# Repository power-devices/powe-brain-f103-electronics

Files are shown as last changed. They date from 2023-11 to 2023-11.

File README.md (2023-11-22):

# Welcome to the Power BrainF103 electronics repository

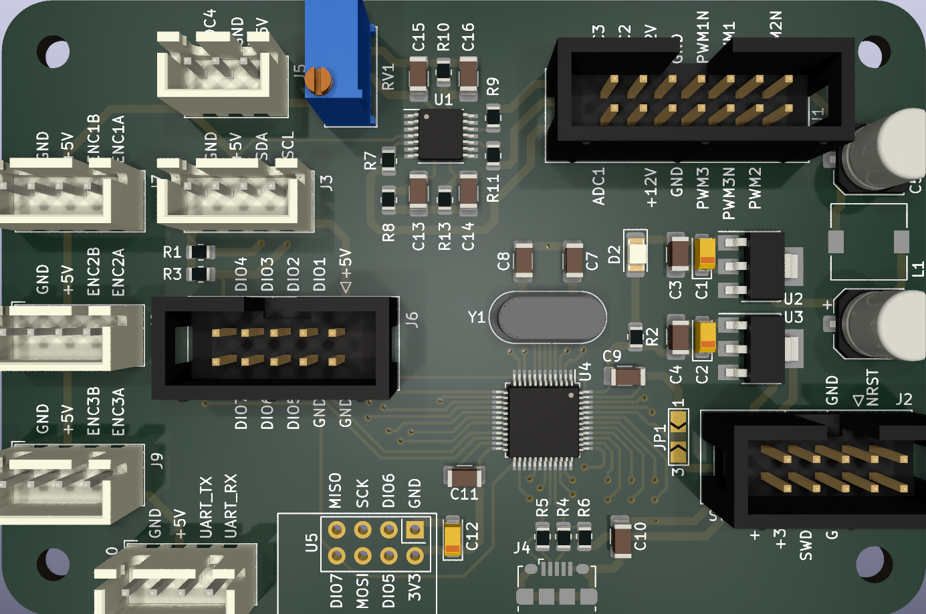
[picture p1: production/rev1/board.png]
REV1 board 3D model


I teach power electronics and I want to provide my students the best experience possible. This is the reason I created this project. I intend to allow people to produce power electronics devices at an extreme low cost. This board required 4 layers, but this is no problem today due to [JLCPCB](https://jlcpcb.com/) or other manufacturers.

So far, the project is divided into 3 pieces:

 1. Power supply: used to delivery power the other boards, it is compatible with mono-three phase up to 220 VAC
 2. Power bullet: a three phase h-bridge, simple as that
 3. Power brain F103: the main controller

# Disclaimer

I provide no warranty at all. Use it at your own risk!

# What will I find here?

You will find the design and production files. To edit the schematic/board you will need to install Kicad. I used version 7 to create this board.

# What can I do with this?

In this repository the board design and production files are stored. You are welcome to download/distribute it, use it, whatever.

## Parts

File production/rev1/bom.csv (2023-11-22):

Designator | Footprint | Quantity | Value | LCSC Part #
C1, C12, C2 | CP_EIA-3216-18_Kemet-A | 3 | 10uF
C10, C11 | 1206 | 2 | 100nF
C13, C14, C15, C16 | 1206 | 4 | 10nF
C3, C4, C9 | 1206 | 3 | 1uF
C5, C6 | CP_Elec_6.3x7.7 | 2 | 100uF
C7, C8 | 1206 | 2 | 22pF
D2 | 1206 | 1 | LED
J1 | IDC-Header_2x07_P2.54mm_Vertical | 1 | Conn_02x07_Odd_Even
J10 | JST_XH_B4B-XH-A_1x04_P2.50mm_Vertical | 1 | UART
J2 | IDC-Header_2x05_P2.54mm_Vertical | 1 | SWD
J3 | JST_XH_B4B-XH-A_1x04_P2.50mm_Vertical | 1 | I2C
J4 | USB_Micro-B_Amphenol_10118194_Horizontal | 1 | USB_B_Micro
J5 | JST_XH_B3B-XH-A_1x03_P2.50mm_Vertical | 1 | ADC_CH4
J6 | IDC-Header_2x05_P2.54mm_Vertical | 1 | GPIO
J7, J8, J9 | JST_XH_B4B-XH-A_1x04_P2.50mm_Vertical | 3 | ENCODER
JP1 | SolderJumper-3_P2.0mm_Open_TrianglePad1.0x1.5mm_NumberLabels | 1 | ~
L1 | L_7.3x7.3_H4.5 | 1 | 100uH
R1, R3 | 0805 | 2 | 3k3
R10, R13, R8 | 0805 | 3 | 91k
R11, R7, R9 | 0805 | 3 | 47k
R2 | 0805 | 1 | 470R
R4, R5 | 0805 | 2 | 22R
R6 | 0805 | 1 | 1k5
RV1 | Potentiometer_Bourns_3296W_Vertical | 1 | 10k
U1 | TSSOP-14_4.4x5mm_P0.65mm | 1 | LM324
U2 | SOT-223-3_TabPin2 | 1 | AMS1117-5.0
U3 | SOT-223-3_TabPin2 | 1 | AMS1117-3.3
U4 | LQFP-48_7x7mm_P0.5mm | 1 | STM32F103C8Tx
U5 | nRF24L01_Breakout | 1 | NRF24L01
Y1 | Crystal_HC49-4H_Vertical | 1 | 16MHz

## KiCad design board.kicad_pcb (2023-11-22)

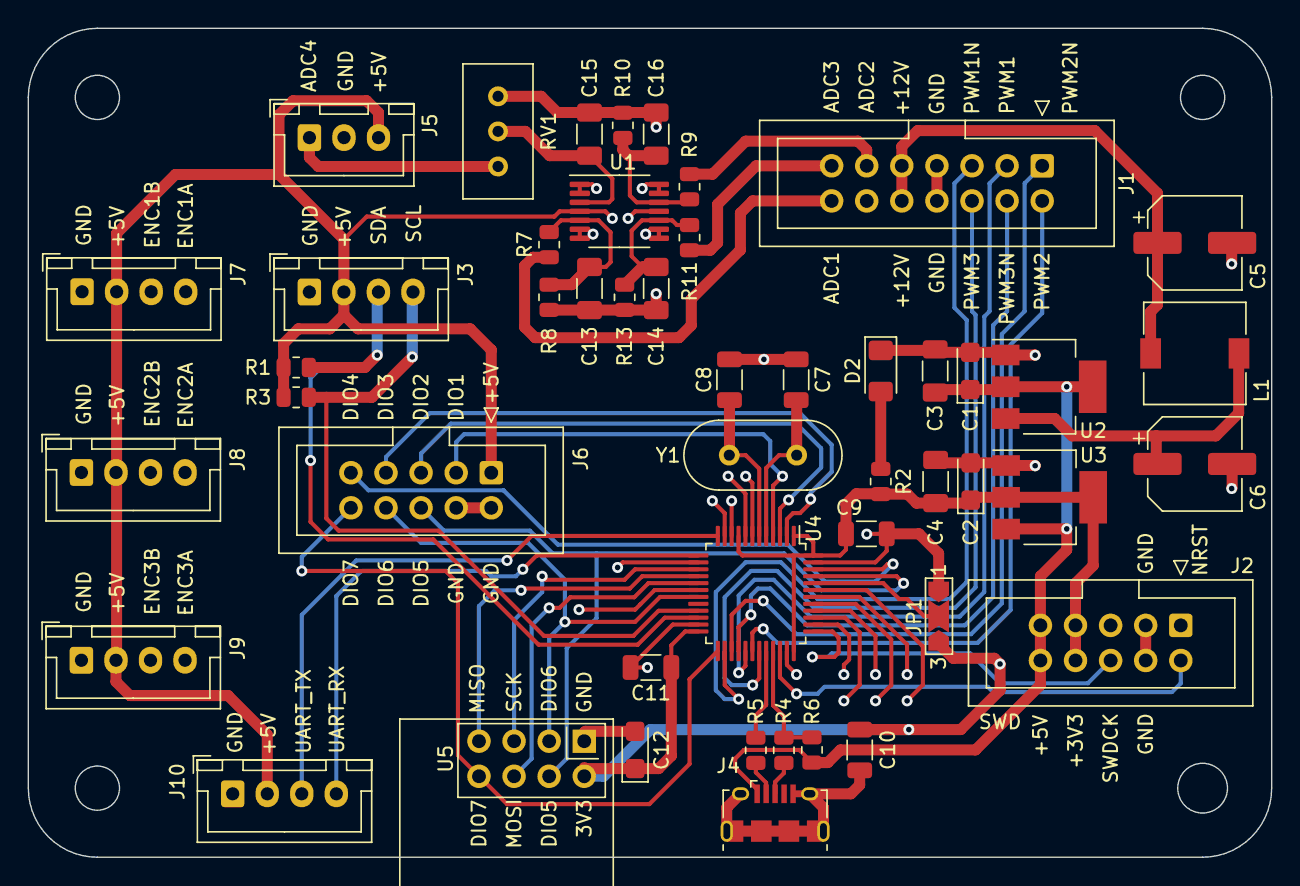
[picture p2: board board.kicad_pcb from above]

Board: 4 copper layers, 90.0 x 60.0 mm, 48 parts (0 on the bottom side), 54 nets.

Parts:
C1, C2, C12: 10uF; CP_EIA-3216-18_Kemet-A
C3, C4: 1uF; C_1206_3216Metric_Pad1.33x1.80mm_HandSolder
C5, C6: 100uF; CP_Elec_6.3x7.7
C7, C8: 22pF; C_1206_3216Metric
C9: 1uF; C_1206_3216Metric
C10, C11: 100nF; C_1206_3216Metric
C13, C14, C15, C16: 10nF; C_1206_3216Metric_Pad1.33x1.80mm_HandSolder
D2: LED; LED_1206_3216Metric_Pad1.42x1.75mm_HandSolder
J1: Conn_02x07_Odd_Even; IDC-Header_2x07_P2.54mm_Vertical
J2: SWD; IDC-Header_2x05_P2.54mm_Vertical
J3: I2C; JST_XH_B4B-XH-A_1x04_P2.50mm_Vertical
J4: USB_B_Micro; USB_Micro-B_Amphenol_10118194_Horizontal
J5: ADC_CH4; JST_XH_B3B-XH-A_1x03_P2.50mm_Vertical
J6: GPIO; IDC-Header_2x05_P2.54mm_Vertical
J7, J8, J9: ENCODER; JST_XH_B4B-XH-A_1x04_P2.50mm_Vertical
J10: UART; JST_XH_B4B-XH-A_1x04_P2.50mm_Vertical
JP1: SolderJumper-3_P2.0mm_Open_TrianglePad1.0x1.5mm_NumberLabels
L1: 100uH; L_7.3x7.3_H4.5
R1, R3: 3k3; R_0805_2012Metric
R2: 470R; R_0805_2012Metric
R4, R5: 22R; R_0805_2012Metric
R6: 1k5; R_0805_2012Metric
R7, R9, R11: 47k; R_0805_2012Metric
R8, R10, R13: 91k; R_0805_2012Metric
RV1: 10k; Potentiometer_Bourns_3296W_Vertical
U1: LM324; TSSOP-14_4.4x5mm_P0.65mm
U2: AMS1117-5.0; SOT-223-3_TabPin2
U3: AMS1117-3.3; SOT-223-3_TabPin2
U4: STM32F103C8Tx; LQFP-48_7x7mm_P0.5mm
U5: NRF24L01; nRF24L01_Breakout
Y1: 16MHz; Crystal_HC49-4H_Vertical

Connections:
+3V3: C2.1, C4.1, C9.1, C10.1, C11.1, C12.1, J2.7, J2.8, JP1.3 (B), R2.2, U3.2 (VO), U4.1 (VBAT), U4.9 (VDDA), U4.24 (VDD), U4.36 (VDD), U4.48 (VDD), U5.2 (VCC)
+5V: C1.1, C3.1, J2.9, J2.10, J3.2, J4.1 (VBUS), J5.3, J6.1, J7.2, J8.2, J9.2, J10.2, R1.1, R3.1, R6.2, U1.4 (V+), U2.2 (VO), U3.3 (VI)
+12V: C6.1, L1.2, U2.3 (VI)
/AD4: J5.1, RV1.1
/ADC_CH1: U1.13 (-), U1.14, U4.10 (PA0)
/ADC_CH2: U1.8, U1.9 (-), U4.11 (PA1)
/ADC_CH3: U1.6 (-), U1.7, U4.14 (PA4)
/ADC_CH4: U1.1, U1.2 (-), U4.18 (PB0)
/BOOT0: JP1.2 (C), U4.44 (BOOT0)
/DRIVE1_GATE_HIGH: J1.3, U4.29 (PA8)
/DRIVE1_GATE_LOW: J1.5, U4.26 (PB13)
/DRIVE1_SENSE_IOUT: J1.14, R7.2
/DRIVE2_GATE_HIGH: J1.2, U4.30 (PA9)
/DRIVE2_GATE_LOW: J1.1, U4.27 (PB14)
/DRIVE2_SENSE_IOUT: J1.11, R9.2
/DRIVE3_GATE_HIGH: J1.6, U4.31 (PA10)
/DRIVE3_GATE_LOW: J1.4, U4.28 (PB15)
/ENC1_CHA: J7.4, U4.42 (PB6)
/ENC1_CHB: J7.3, U4.43 (PB7)
/ENC2_CHA: J8.4, U4.38 (PA15)
/ENC2_CHB: J8.3, U4.39 (PB3)
/ENC3_CHA: J9.4, U4.40 (PB4)
/ENC3_CHB: J9.3, U4.41 (PB5)
/GPIO_CH1: J6.3, U4.4 (PC15)
/GPIO_CH2: J6.5, U4.3 (PC14)
/GPIO_CH3: J6.7, U4.2 (PC13)
/GPIO_CH4: J6.9, U4.46 (PB9)
/GPIO_CH5: J6.6, U4.45 (PB8), U5.4 (~CSN)
/GPIO_CH6: J6.8, U4.19 (PB1), U5.3 (CE)
/GPIO_CH7: J6.10, U4.25 (PB12), U5.8 (IRQ)
/I2C_SCL: J3.4, R3.2, U4.21 (PB10)
/I2C_SDA: J3.3, R1.2, U4.22 (PB11)
/NRST: J2.1, U4.7 (NRST)
/POWER_12V: C5.1, J1.9, J1.10, L1.1
/SENSE_VBUS: J1.13, R11.2
/SPI_MISO: U4.16 (PA6), U5.7 (MISO)
/SPI_MOSI: U4.17 (PA7), U5.6 (MOSI)
/SPI_SCK: U4.15 (PA5), U5.5 (SCK)
/SWDCK: J2.6, U4.37 (PA14)
/SWDIO: J2.2, U4.34 (PA13)
/UART_RX: J10.4, U4.13 (PA3)
/UART_TX: J10.3, U4.12 (PA2)
/USB+: R4.1, R6.1, U4.33 (PA12)
/USB-: R5.1, U4.32 (PA11)
/XTAL1: C7.1, U4.5 (PD0), Y1.1
/XTAL2: C8.1, U4.6 (PD1), Y1.2
GND: C1.2, C2.2, C3.2, C4.2, C5.2, C6.2, C7.2, C8.2, C9.2, C10.2, C11.2, C12.2, C13.2, C14.2, C15.2, C16.2, D2.1 (K), J1.7, J1.8, J2.3, J2.4, J3.1, J4.5 (GND), J4.6 (Shield), J5.2, J6.2, J6.4, J7.1, J8.1, J9.1, J10.1, JP1.1 (A), R8.2, R10.2, R13.2, RV1.3, U1.11 (V-), U2.1 (GND), U3.1 (GND), U4.8 (VSSA), U4.23 (VSS), U4.35 (VSS), U4.47 (VSS), U5.1 (GND)
unnamed: D2.2 (A), R2.1
unnamed: J4.3 (D+), R4.2
unnamed: J4.2 (D-), R5.2
unnamed: C15.1, RV1.2, U1.3 (+)
unnamed: C13.1, R7.1, R8.1, U1.5 (+)
unnamed: C14.1, R11.1, R13.1, U1.10 (+)
unnamed: C16.1, R9.1, R10.1, U1.12 (+)
